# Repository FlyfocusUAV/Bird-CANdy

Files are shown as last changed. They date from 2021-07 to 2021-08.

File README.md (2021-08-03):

# Bird-CANdy

[][cc-by-sa] 

<hr>

PCB designed mainly as a universal [UAVCAN](https://uavcan.org/) sensor node which may also be used as a generic CAN interfacing device.

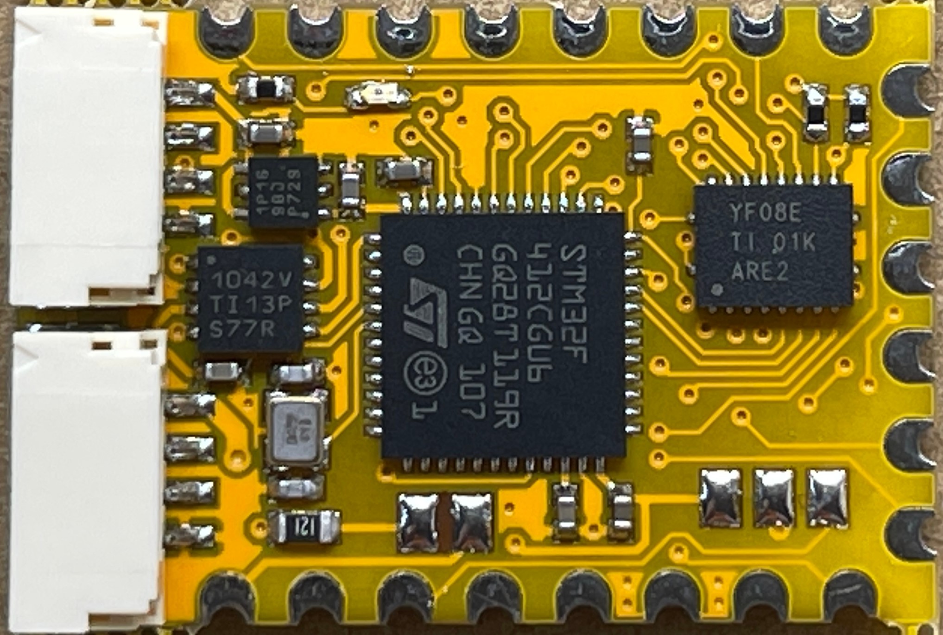
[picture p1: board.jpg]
Board top photo


<br>

# What's UAVCAN Node? #
UAVCAN Node is a device that speaks UAVCAN protocol which is usually used to exchange data between autopilot (e.g. The Cube or Pixhawk running Ardupilot software)
and peripherals like GPS, Compass, LEDs, etc.

Since UAVCAN uses CAN inteface it allows for much longer wires than in case of I2C/SPI/UART/etc. and interference free data exchange due to the use of differential pairs.

# Advantages of Bird CANdy PCB #
PCB was designed with hobbyist, DIYers and researchers in mind.
* Fully Open Source Hardware for non-commercial use
* Only 2 copper layers for cheap production
* 3.3V or 5V selectable outputs
* JST-GH connectors (fully compatible with [The Cube Autopilot](https://github.com/proficnc/The-Cube))
* Supports all [Ardupilot](https://ardupilot.org/) peripherals like GPS, Compass, Baro, IMU, LEDs, etc, as well as PWM Servo output.

# What about the software? #
PCB can run [AP_Periph](https://github.com/ArduPilot/ardupilot/tree/master/Tools/AP_Periph) or your own software written for STM32 microcontroller.

# Pinout #
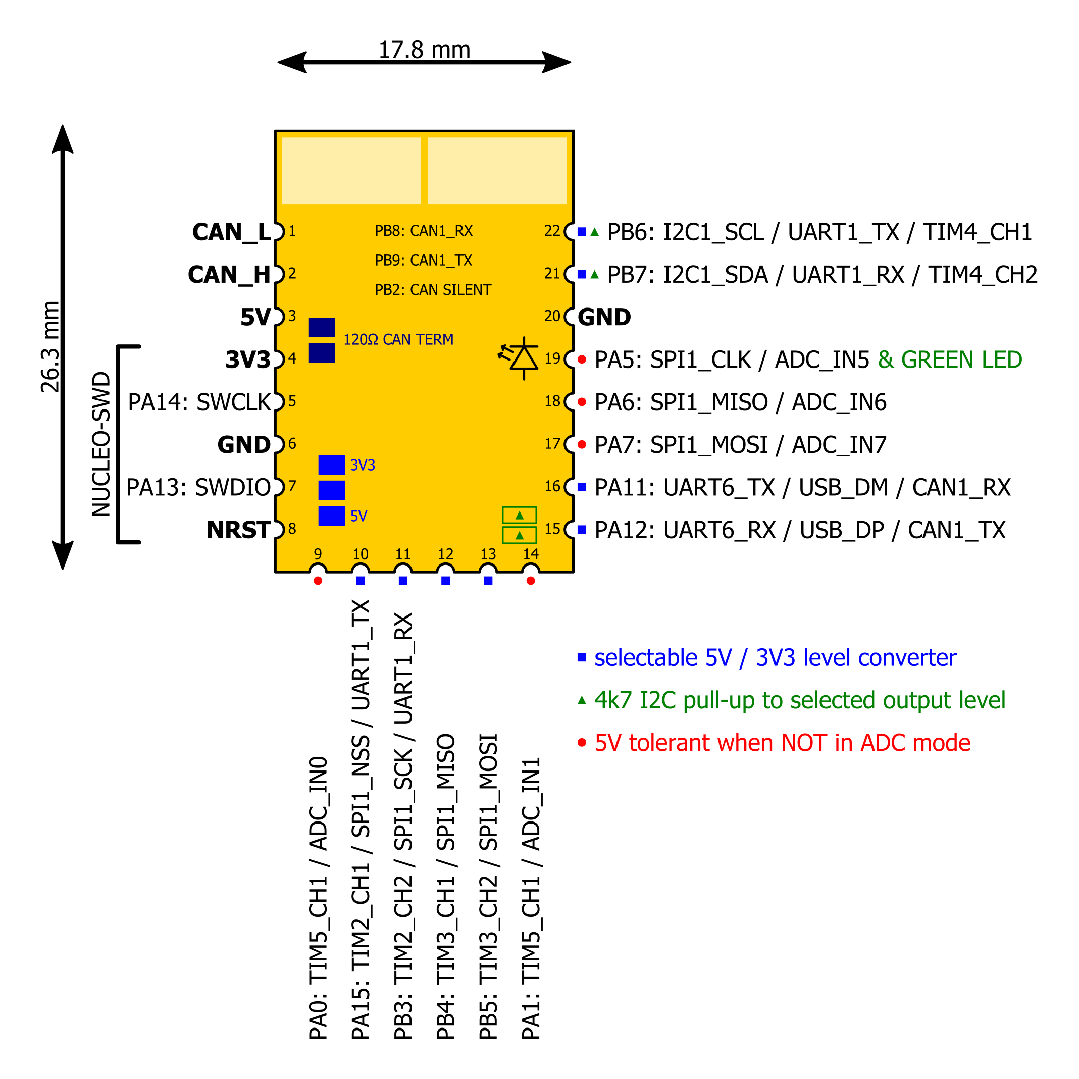
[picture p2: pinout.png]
Pinout guide


# Commercial license #
If You need a commercial license please send us an email to contact@flyfocus.pl 
<!-- <a href="https://www.linkedin.com/company/flyfocus/"> ![alt text](https://img.shields.io/badge/-LinkedIn-a8400e?style=flat&logo=linkedIn)</a>
<a href="https://www.facebook.com/flyfocusUAV"> ![alt text](https://img.shields.io/badge/-Facebook-a8400e?style=flat&logo=Facebook)</a> -->

[cc-by-sa]: https://creativecommons.org/licenses/by-sa/4.0/
[cc-by-shield]: https://img.shields.io/badge/License-CC%20BY%20%20SA%204.0-a8400e

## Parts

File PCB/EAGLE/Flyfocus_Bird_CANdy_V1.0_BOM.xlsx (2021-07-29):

Item # | Designator | QTY | Mfg Part # | Value/Description | Package
1 | C4,C5 | 2 | generic MLCC capacitor | 100n | 0402
2 | R1 | 1 | smd thick film >=0.2W resistor | 120R thick film: >=0.2W | 0603
3 | C2,C3 | 2 | generic MLCC capacitor | 10p | 0402
4 | C6, C7, C8 | 3 | generic MLCC capacitor | 1u | 0402
5 | U$1 | 1 | ABM11AIG-16.000MHZ-8-1Z-T or similar | 16MHZ | 2x1.6mm crystal
6 | C1,C9 | 2 | generic MLCC capacitor | 2u2 | 0402
7 | R2, R3 | 2 | generic smd resistor | 4k7 | 0402
8 | J1, J2 | 2 | SM04B-GHS-TB(LF)(SN) | JST-GH connector
9 | U1 | 1 | STM32F412CEU6/STM32F412CGU6 |  | 48-UFQFPN
10 | U2 | 1 | TJA1051TK/3/1J or TCAN1042HVDRBTQ1 |  | 8-VDFN
11 | U4 | 1 | TPS74633 |  | 6-WSON
12 | U3 | 1 | TXS0108ERGYR |  | 20-VFQFN
13 | D1 | 1 | generic 0402 LED - GREEN |  | 0402
14 | R4 | 1 | generic smd resistor | 33R | 0402

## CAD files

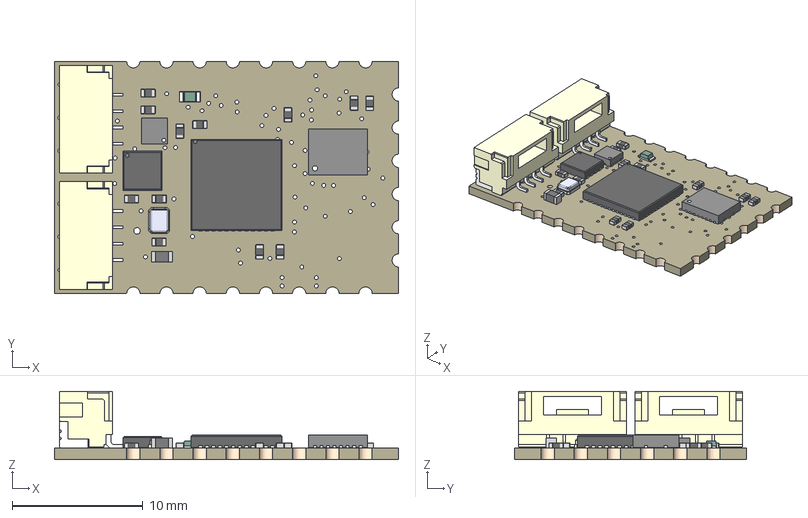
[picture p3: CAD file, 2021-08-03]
PCB/Flyfocus_Bird_CANdy_V1.0.step
26.3 x 17.8 x 5.22 mm
Board
STM32F412CEU6TRUFQFPN-48_7X7X0P55MM-M
SM04B-GHS-TB(LF)(SN)- x 2
TJA1051TK/3/1J
TPS74633PQWDRVRQ1
TXS0108ERGYR
Ferrite
Contact x 2
2X1.6_CRYSTAL
MA08-1
MA08-1 (1)
MA06-1
33R x 12
SJ
SJ_2

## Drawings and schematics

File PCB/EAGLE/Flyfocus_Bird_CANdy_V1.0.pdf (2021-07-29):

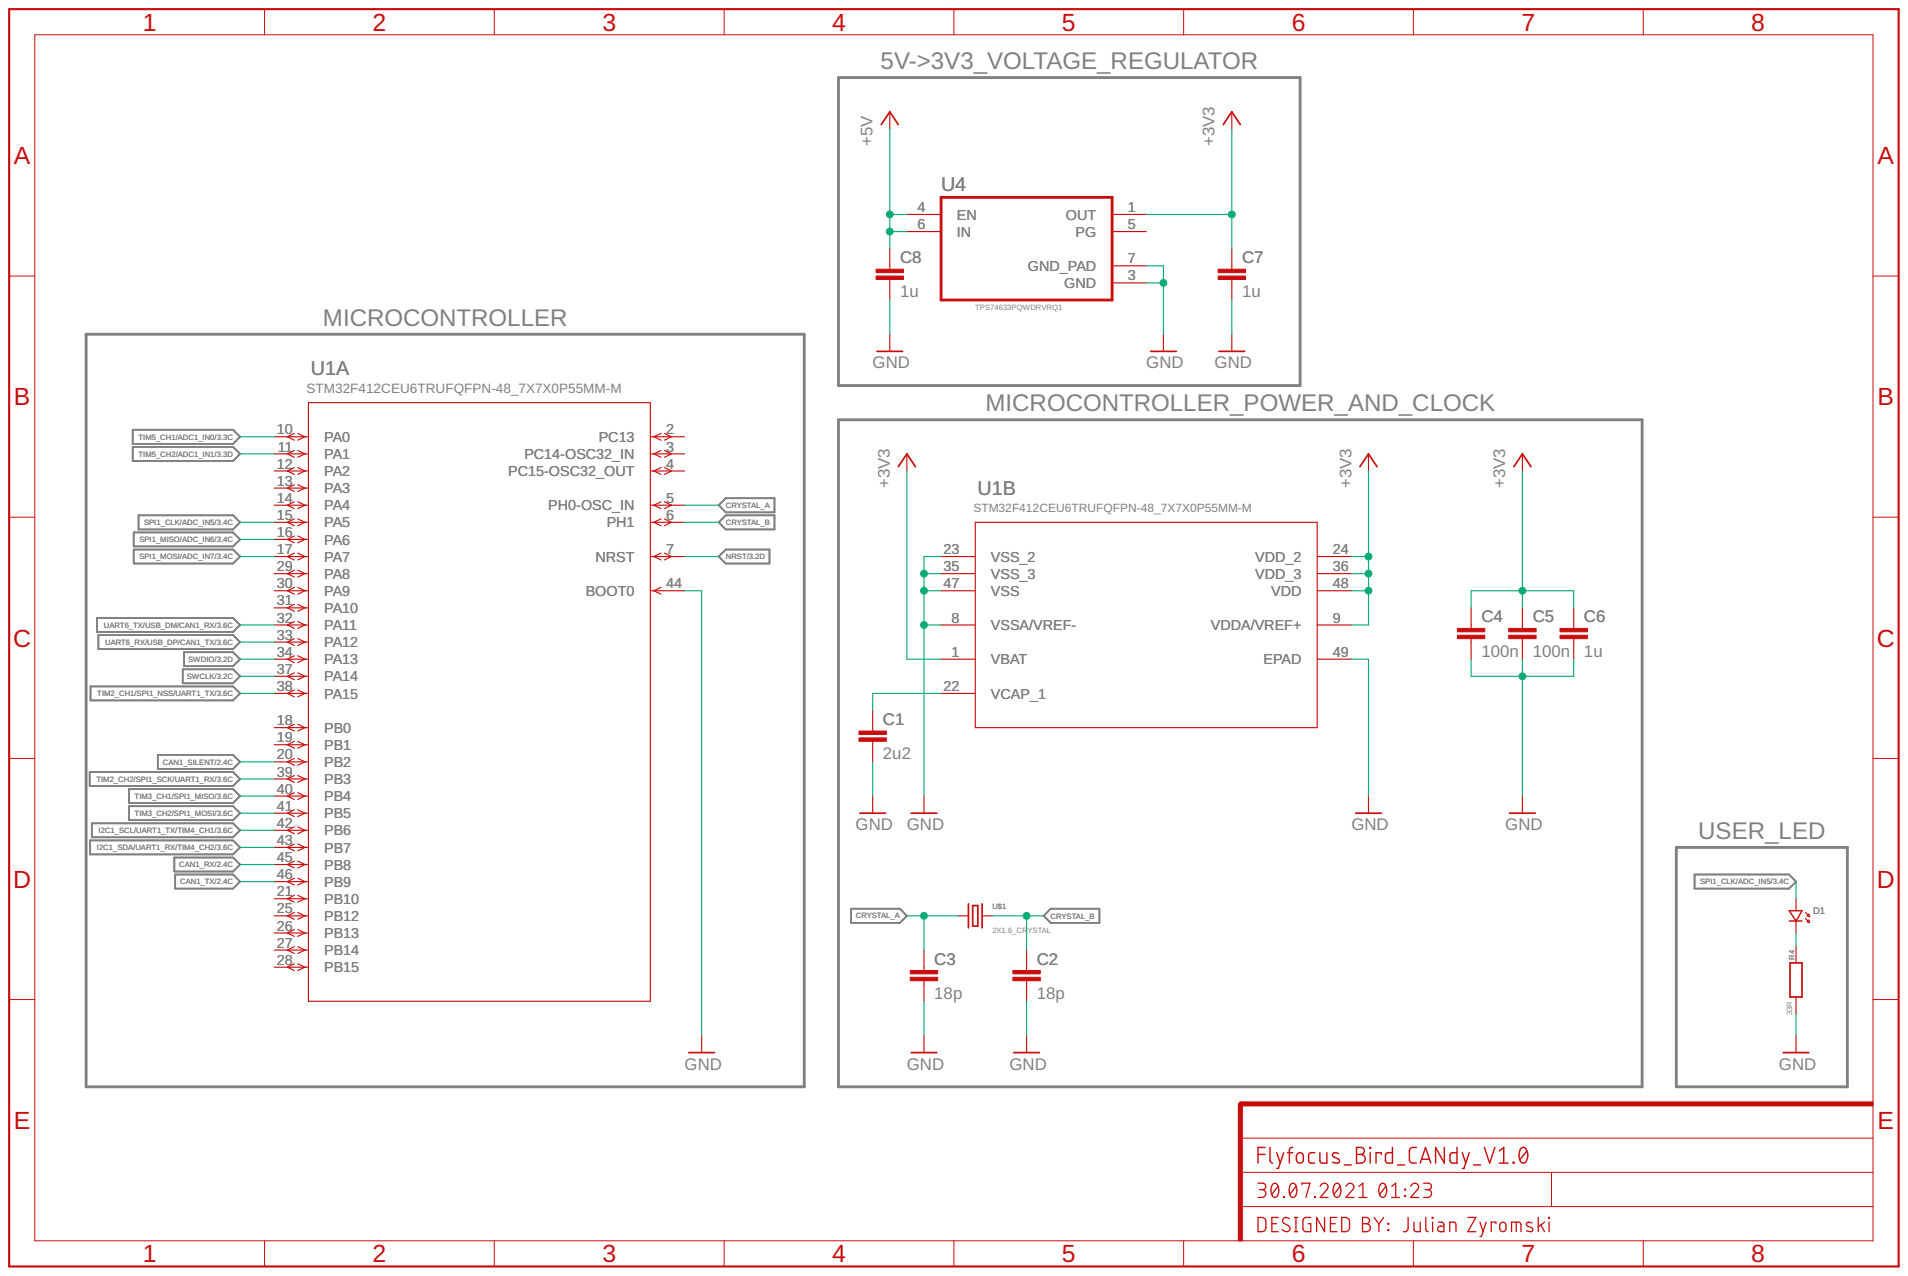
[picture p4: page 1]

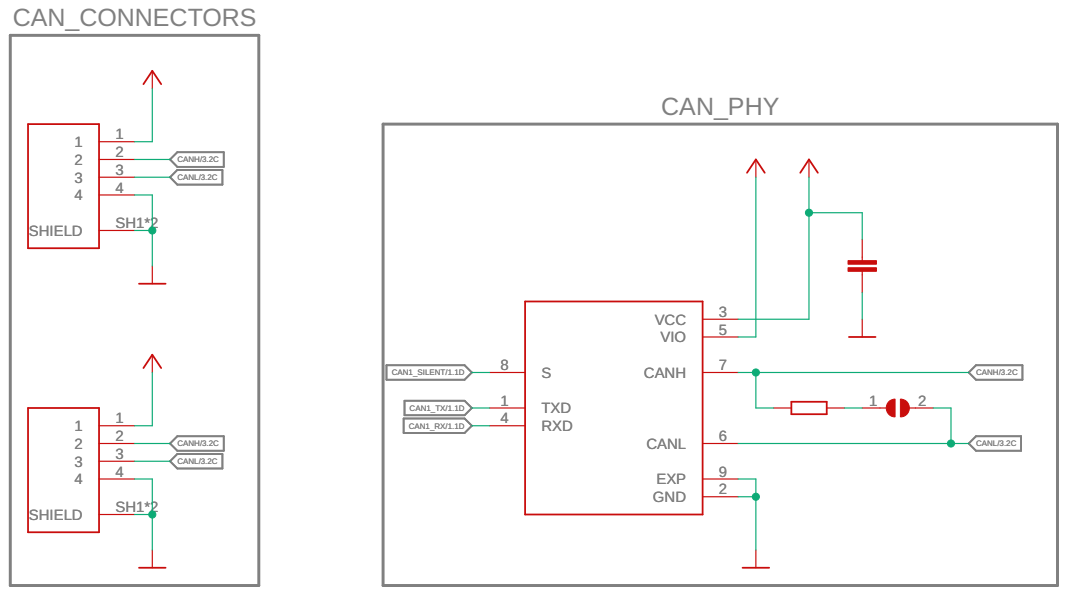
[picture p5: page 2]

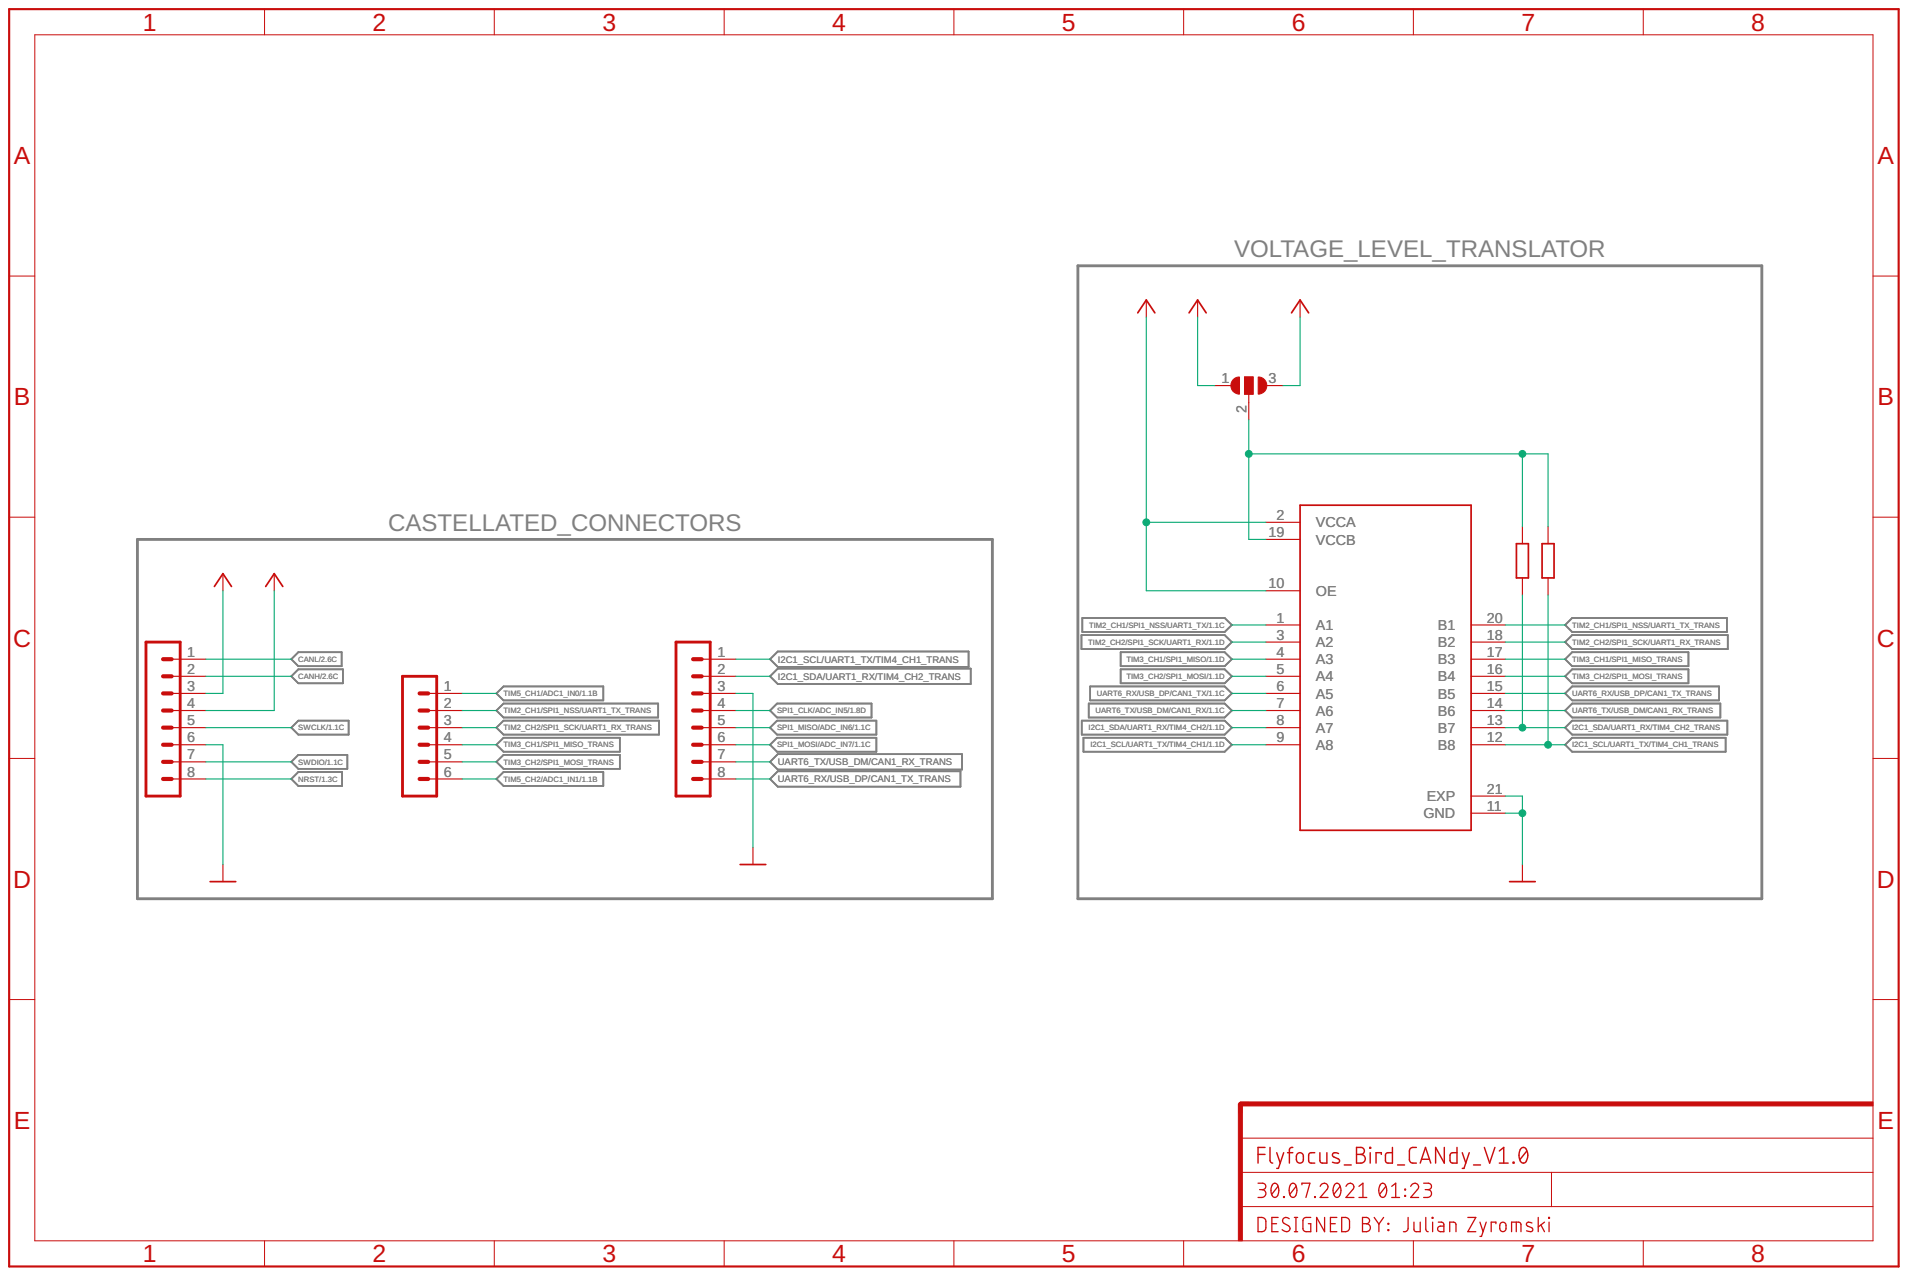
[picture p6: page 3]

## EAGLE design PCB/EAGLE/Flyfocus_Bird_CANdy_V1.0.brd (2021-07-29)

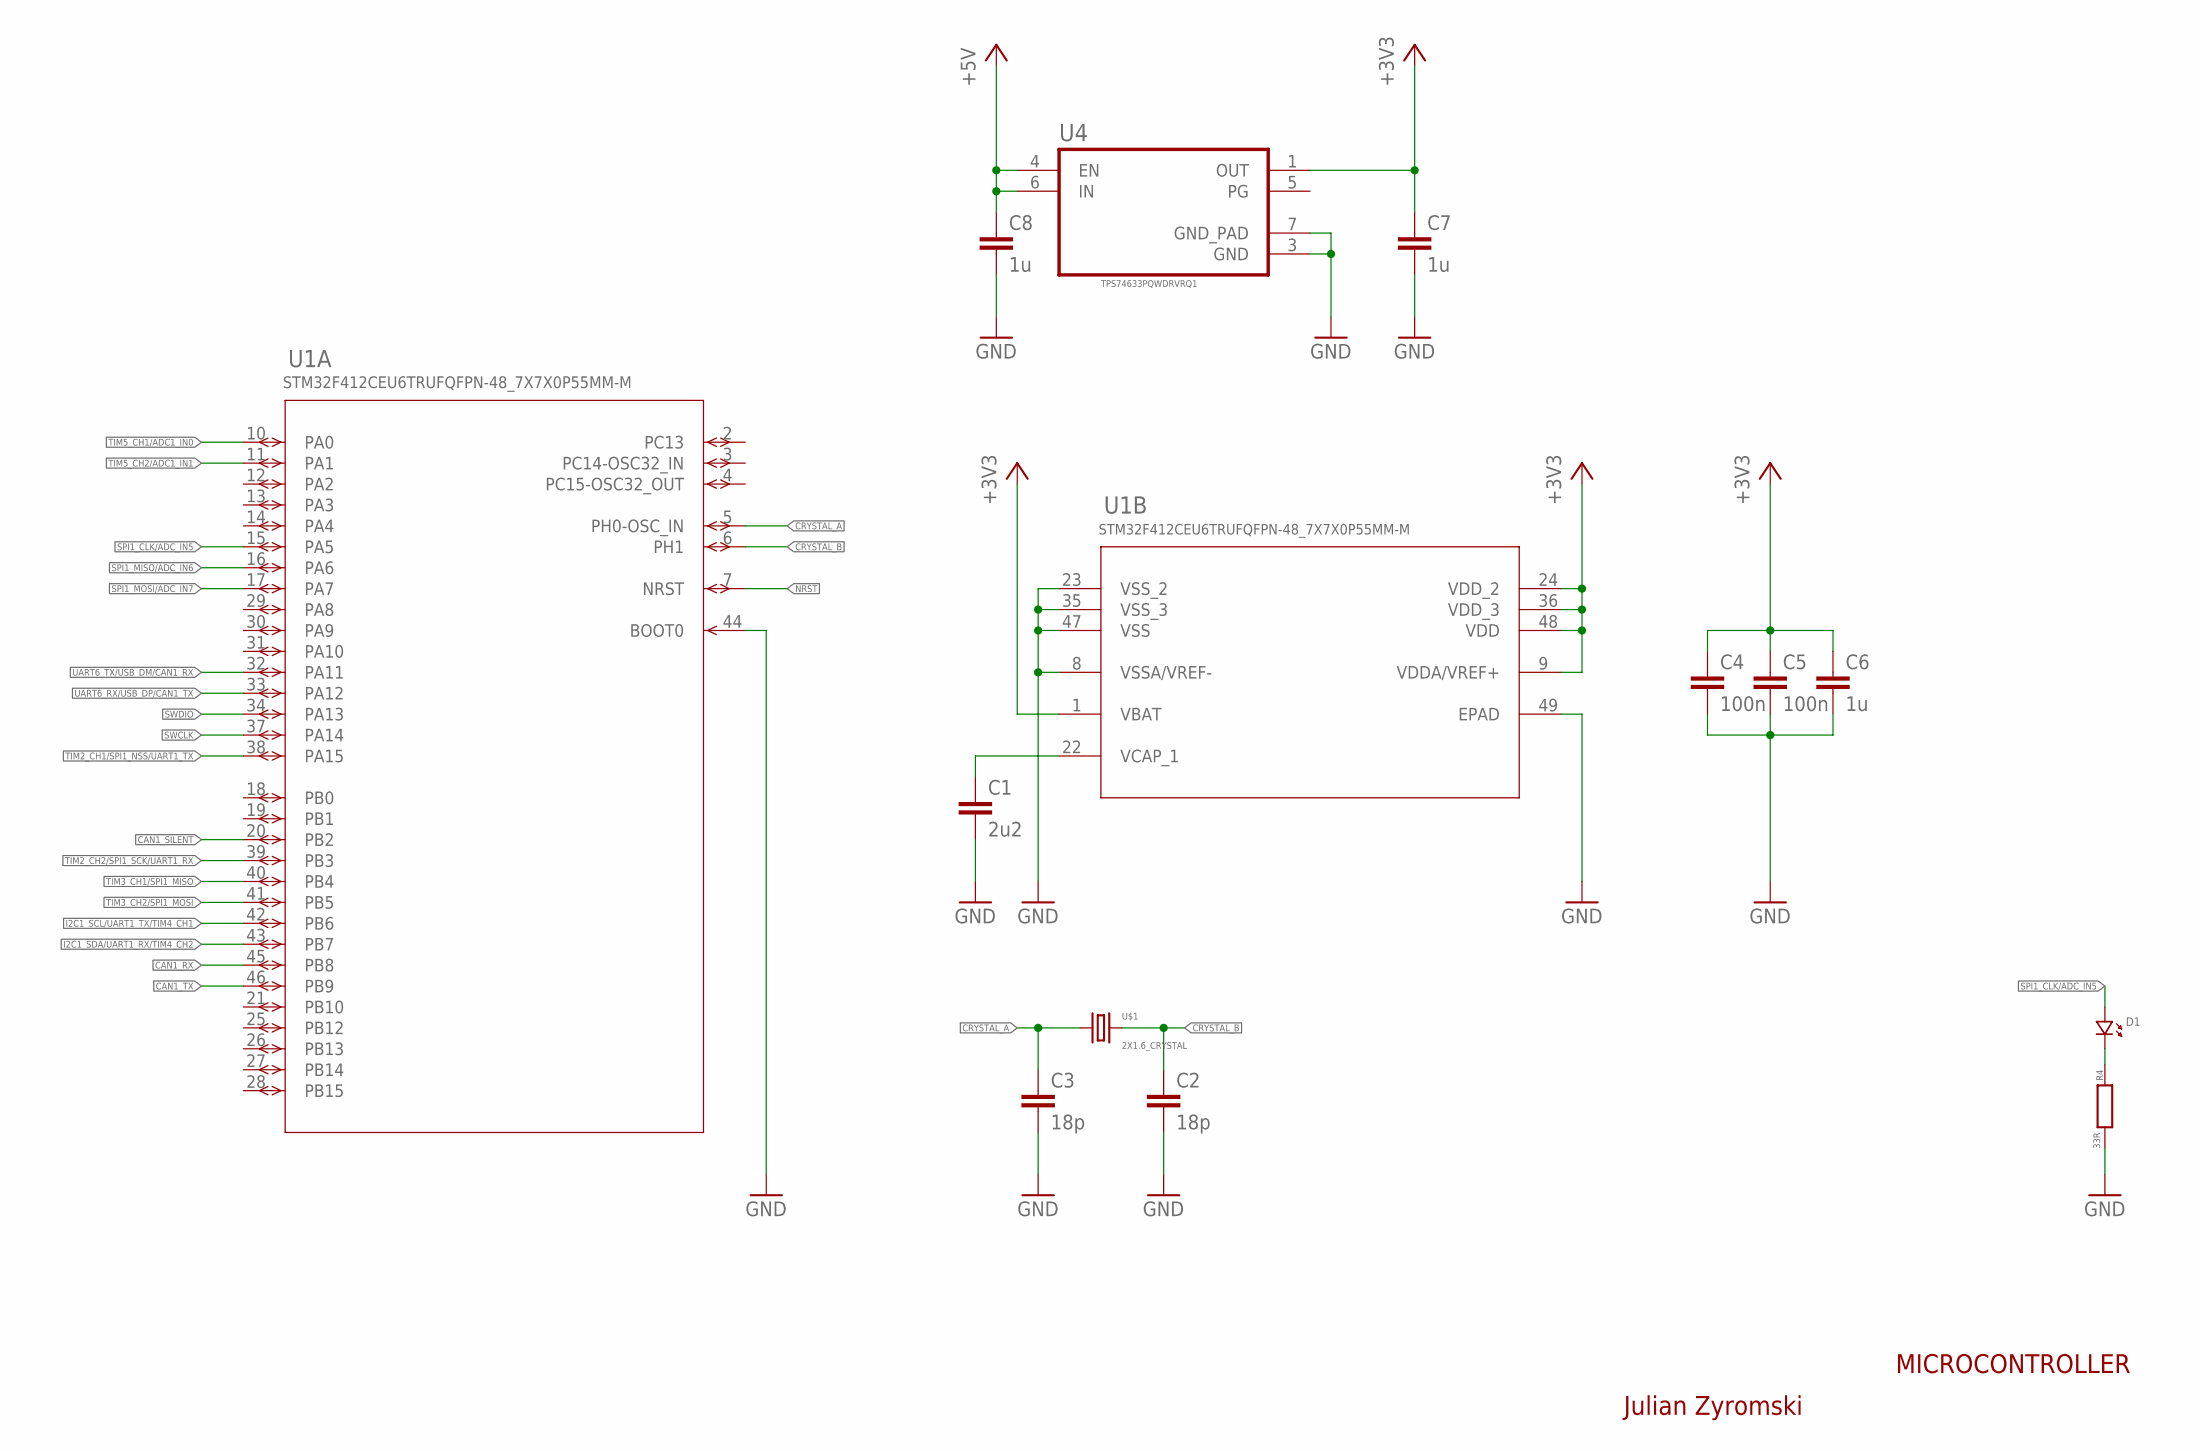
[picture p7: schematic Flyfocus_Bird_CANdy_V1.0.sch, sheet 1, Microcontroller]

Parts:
C1: 2u2; R0402
C2, C3: 18p; R0402
C4, C5: 100n; R0402
C6, C7, C8: 1u; R0402
D1: LED.0402; 0402.LED
R4: 33R; R0402
U1: STM32F412CEU6TRUFQFPN-48_7X7X0P55MM-M; UFQFPN-48_7X7X0P55MM-M
U4: TPS74633PQWDRVRQ1; SON65P200X200X80-7N
U$1: 2X1.6_CRYSTAL; OSC_FA-128_16MHZ

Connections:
+3V3: C4.1, C5.1, C6.1, C7.1, U1.1 (VBAT), U1.9 (VDDA/VREF+), U1.24 (VDD_2), U1.36 (VDD_3), U1.48 (VDD), U4.1 (OUT); also elsewhere on the board
+5V: C8.1, U4.4 (EN), U4.6 (IN); also elsewhere on the board
CAN1_RX: U1.45 (PB8); also elsewhere on the board
CAN1_SILENT: U1.20 (PB2); also elsewhere on the board
CAN1_TX: U1.46 (PB9); also elsewhere on the board
CRYSTAL_A: C3.1, U1.5 (PH0-OSC_IN), U$1.1
CRYSTAL_B: C2.1, U1.6 (PH1), U$1.3 (2)
GND: C1.2, C2.2, C3.2, C4.2, C5.2, C6.2, C7.2, C8.2, R4.2, U1.8 (VSSA/VREF-), U1.23 (VSS_2), U1.35 (VSS_3), U1.44 (BOOT0), U1.47 (VSS), U1.49 (EPAD), U4.3 (GND), U4.7 (GND_PAD); also elsewhere on the board
I2C1_SCL/UART1_TX/TIM4_CH1: U1.42 (PB6); also elsewhere on the board
I2C1_SDA/UART1_RX/TIM4_CH2: U1.43 (PB7); also elsewhere on the board
unnamed: C1.1, U1.22 (VCAP_1)
unnamed: D1.P$2 (2), R4.1
NRST: U1.7 (NRST); also elsewhere on the board
SPI1_CLK/ADC_IN5: D1.P$1 (1), U1.15 (PA5); also elsewhere on the board
SPI1_MISO/ADC_IN6: U1.16 (PA6); also elsewhere on the board
SPI1_MOSI/ADC_IN7: U1.17 (PA7); also elsewhere on the board
SWCLK: U1.37 (PA14); also elsewhere on the board
SWDIO: U1.34 (PA13); also elsewhere on the board
TIM2_CH1/SPI1_NSS/UART1_TX: U1.38 (PA15); also elsewhere on the board
TIM2_CH2/SPI1_SCK/UART1_RX: U1.39 (PB3); also elsewhere on the board
TIM3_CH1/SPI1_MISO: U1.40 (PB4); also elsewhere on the board
TIM3_CH2/SPI1_MOSI: U1.41 (PB5); also elsewhere on the board
TIM5_CH1/ADC1_IN0: U1.10 (PA0); also elsewhere on the board
TIM5_CH2/ADC1_IN1: U1.11 (PA1); also elsewhere on the board
UART6_RX/USB_DP/CAN1_TX: U1.33 (PA12); also elsewhere on the board
UART6_TX/USB_DM/CAN1_RX: U1.32 (PA11); also elsewhere on the board

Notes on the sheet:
Julian Zyromski
MICROCONTROLLER

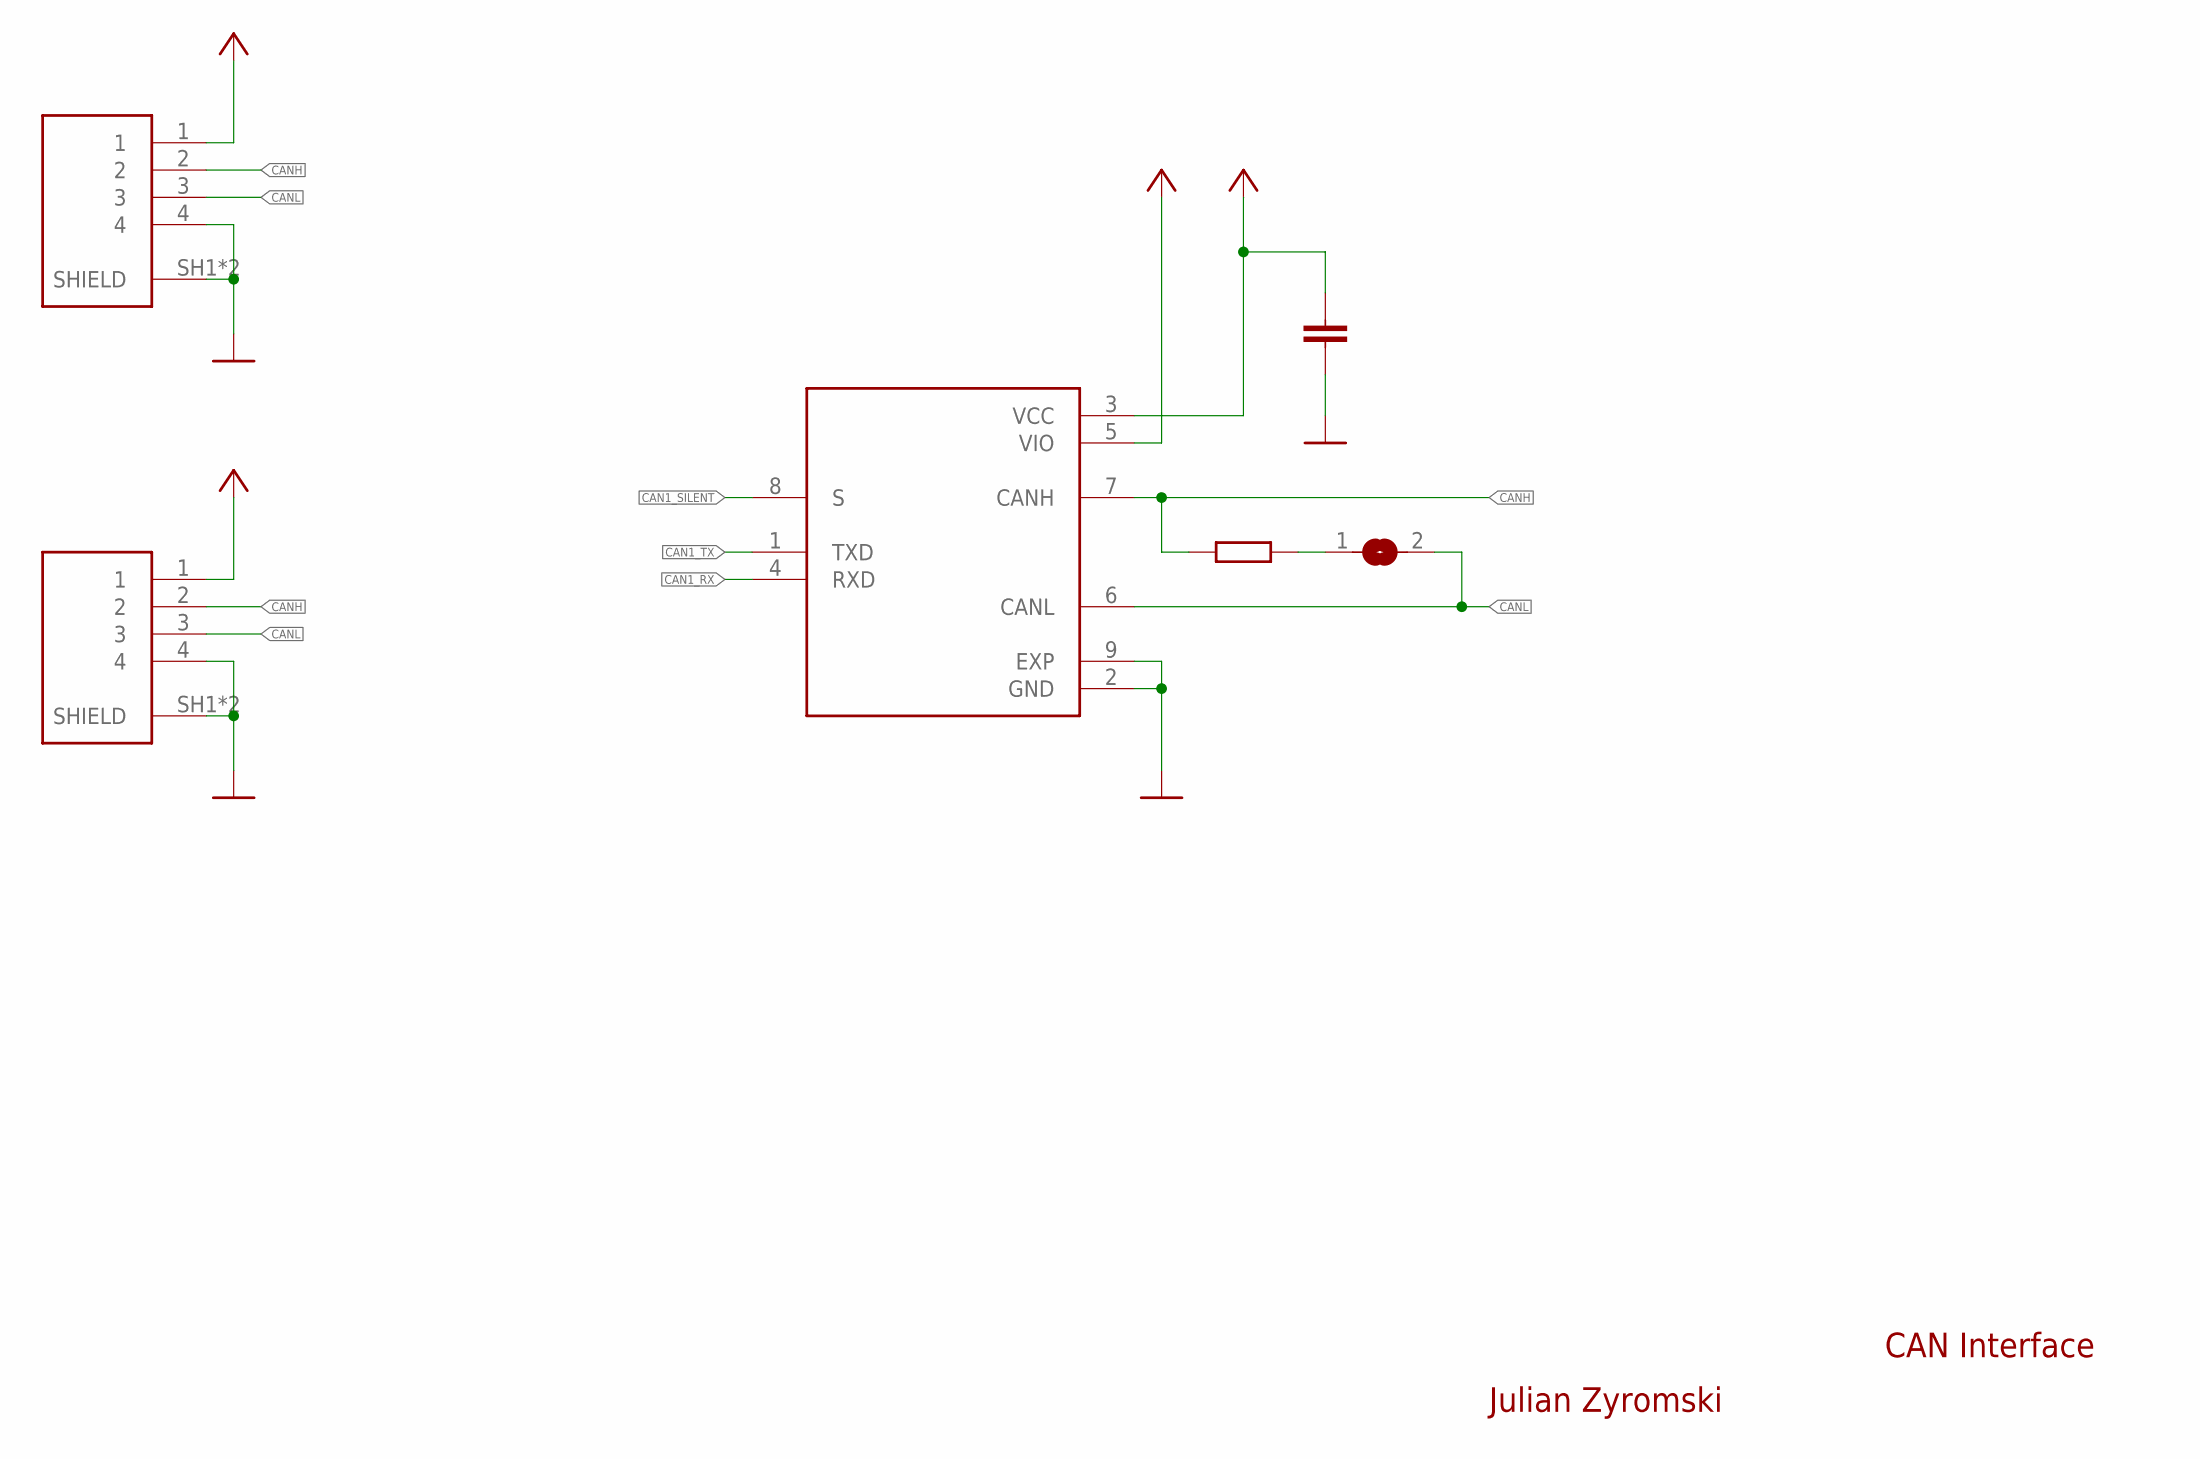
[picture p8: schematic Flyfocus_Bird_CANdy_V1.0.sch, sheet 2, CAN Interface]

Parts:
C9: 2u2; R0402
J1, J2: SM04B-GHS-TB(LF)(SN)-; JST_SM04B-GHS-TB(LF)(SN)-
R1: 120R/thick_film; 0603
SJ1: SJ
U2: TJA1051TK/3/1J; SON65P300X300X95-8N

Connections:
+3V3: U2.5 (VIO); also elsewhere on the board
+5V: C9.1, J1.1, J2.1, U2.3 (VCC); also elsewhere on the board
CAN1_RX: U2.4 (RXD); also elsewhere on the board
CAN1_SILENT: U2.8 (S); also elsewhere on the board
CAN1_TX: U2.1 (TXD); also elsewhere on the board
CANH: J1.2, J2.2, R1.P$1 (1), U2.7 (CANH); also elsewhere on the board
CANL: J1.3, J2.3, SJ1.2, U2.6 (CANL); also elsewhere on the board
GND: C9.2, J1.4, J1.SH1 (SHIELD), J1.SH2 (SHIELD), J2.4, J2.SH1 (SHIELD), J2.SH2 (SHIELD), U2.2 (GND), U2.9 (EXP); also elsewhere on the board
unnamed: R1.P$2 (2), SJ1.1

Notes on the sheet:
Julian Zyromski
CAN Interface

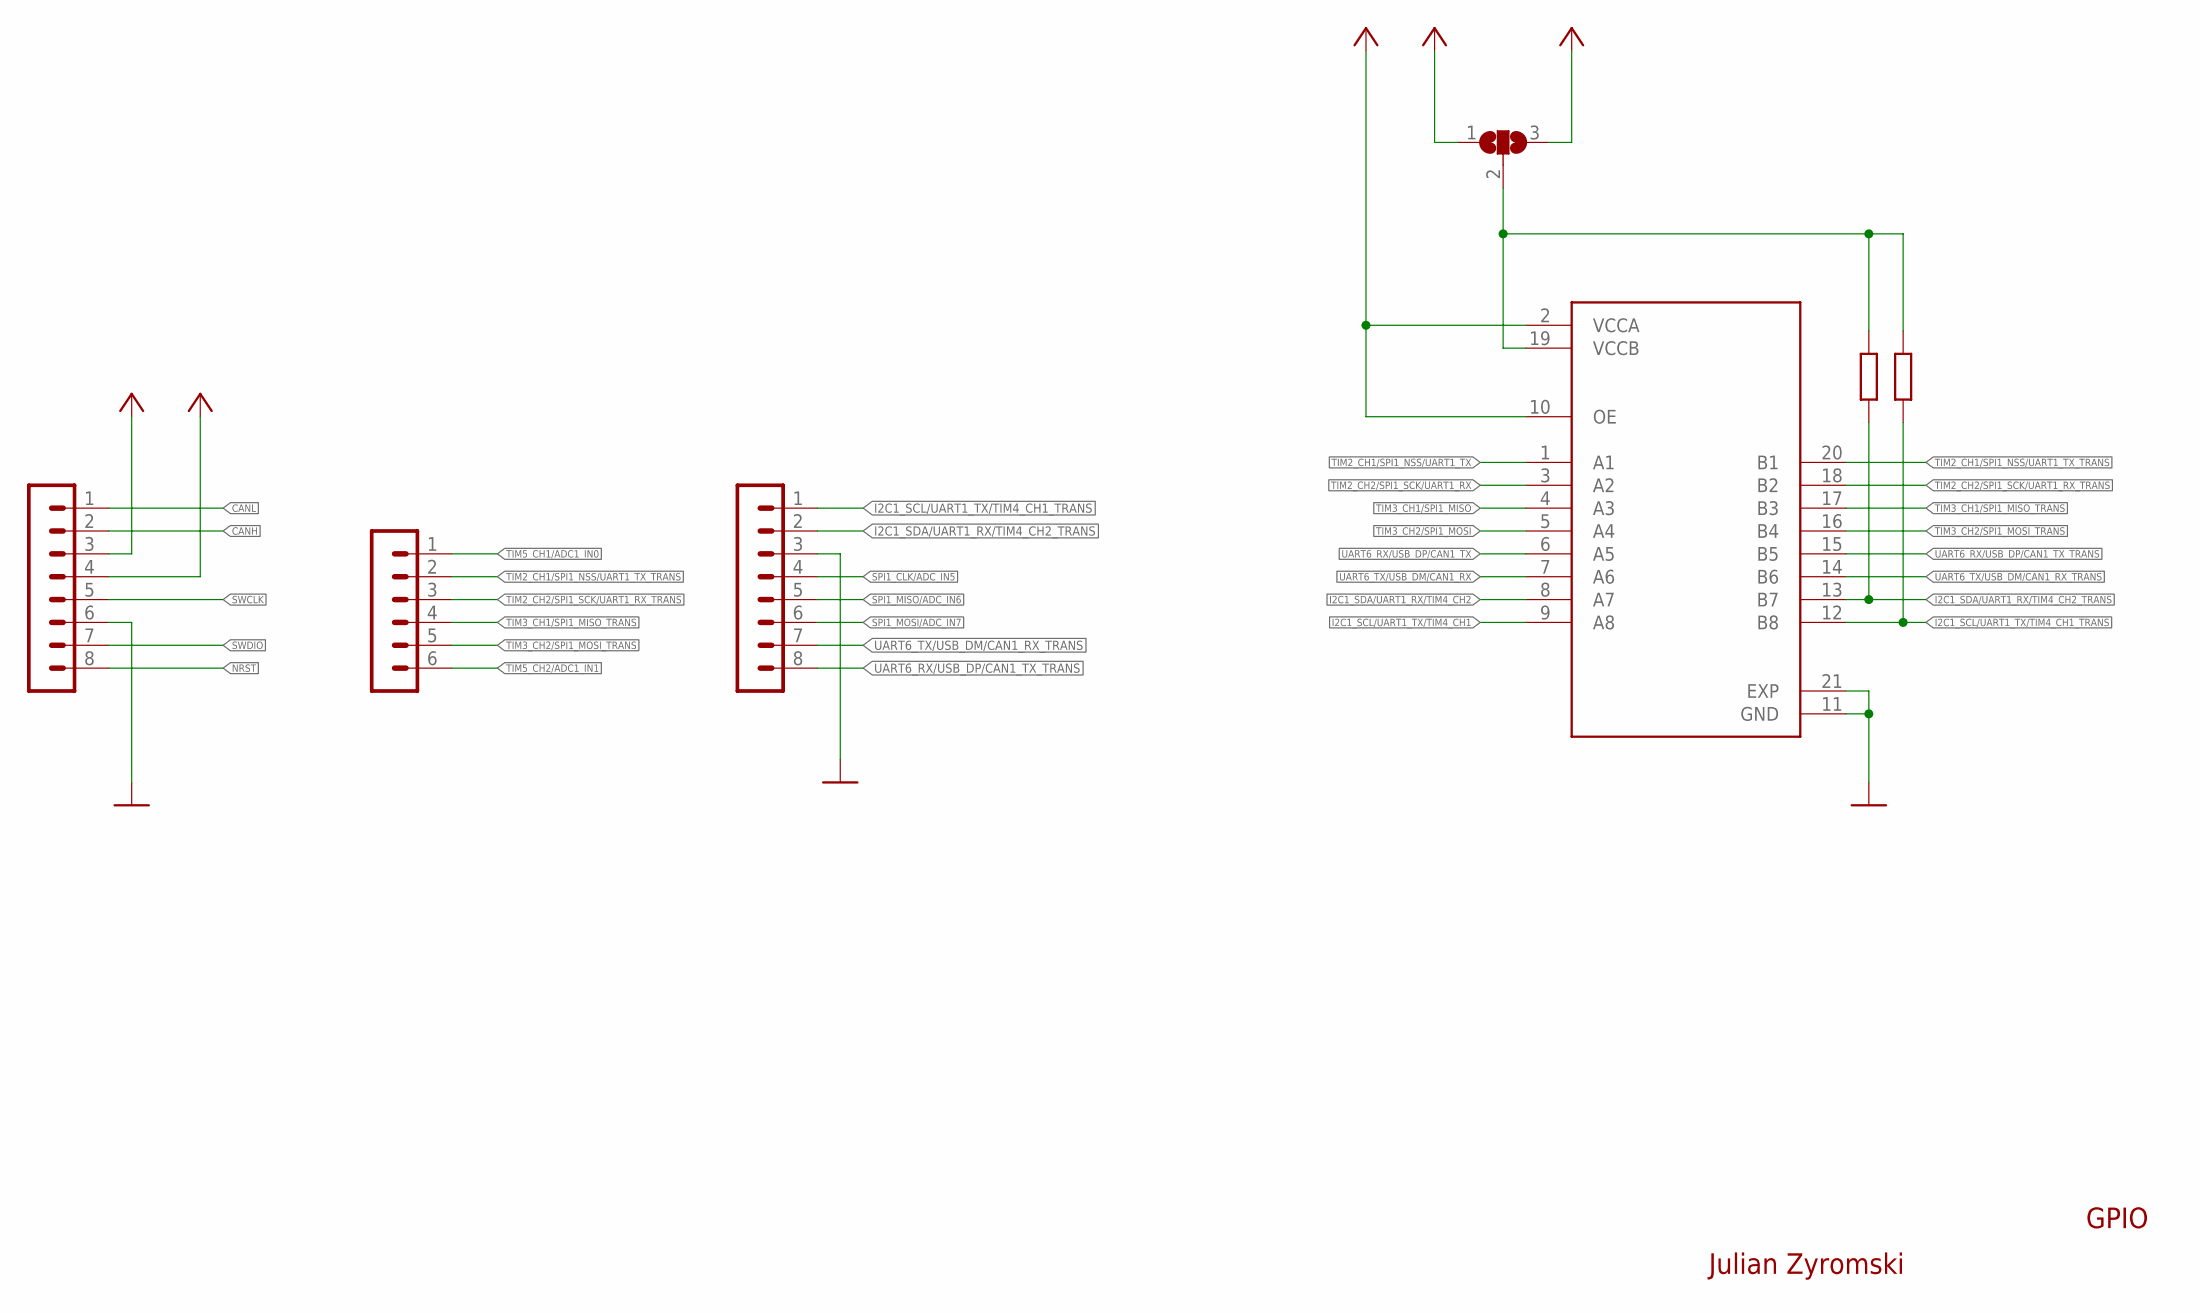
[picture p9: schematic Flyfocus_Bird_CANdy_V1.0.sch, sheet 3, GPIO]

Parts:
R2, R3: 4k7; R0402
SJ2: SJ2W; SJ_2
SV1, SV2: MA08-1
SV3: MA06-1
U3: TXS0108ERGYR; IC_TXS0108ERGYR

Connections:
+3V3: SJ2.1, SV1.4, U3.2 (VCCA), U3.10 (OE); also elsewhere on the board
+5V: SJ2.3, SV1.3; also elsewhere on the board
CANH: SV1.2; also elsewhere on the board
CANL: SV1.1; also elsewhere on the board
GND: SV1.6, SV2.3, U3.11 (GND), U3.21 (EXP); also elsewhere on the board
I2C1_SCL/UART1_TX/TIM4_CH1: U3.9 (A8); also elsewhere on the board
I2C1_SCL/UART1_TX/TIM4_CH1_TRANS: R3.1, SV2.1, U3.12 (B8)
I2C1_SDA/UART1_RX/TIM4_CH2: U3.8 (A7); also elsewhere on the board
I2C1_SDA/UART1_RX/TIM4_CH2_TRANS: R2.1, SV2.2, U3.13 (B7)
unnamed: R2.2, R3.2, SJ2.2, U3.19 (VCCB)
NRST: SV1.8; also elsewhere on the board
SPI1_CLK/ADC_IN5: SV2.4; also elsewhere on the board
SPI1_MISO/ADC_IN6: SV2.5; also elsewhere on the board
SPI1_MOSI/ADC_IN7: SV2.6; also elsewhere on the board
SWCLK: SV1.5; also elsewhere on the board
SWDIO: SV1.7; also elsewhere on the board
TIM2_CH1/SPI1_NSS/UART1_TX: U3.1 (A1); also elsewhere on the board
TIM2_CH1/SPI1_NSS/UART1_TX_TRANS: SV3.2, U3.20 (B1)
TIM2_CH2/SPI1_SCK/UART1_RX: U3.3 (A2); also elsewhere on the board
TIM2_CH2/SPI1_SCK/UART1_RX_TRANS: SV3.3, U3.18 (B2)
TIM3_CH1/SPI1_MISO: U3.4 (A3); also elsewhere on the board
TIM3_CH1/SPI1_MISO_TRANS: SV3.4, U3.17 (B3)
TIM3_CH2/SPI1_MOSI: U3.5 (A4); also elsewhere on the board
TIM3_CH2/SPI1_MOSI_TRANS: SV3.5, U3.16 (B4)
TIM5_CH1/ADC1_IN0: SV3.1; also elsewhere on the board
TIM5_CH2/ADC1_IN1: SV3.6; also elsewhere on the board
UART6_RX/USB_DP/CAN1_TX: U3.6 (A5); also elsewhere on the board
UART6_RX/USB_DP/CAN1_TX_TRANS: SV2.8, U3.15 (B5)
UART6_TX/USB_DM/CAN1_RX: U3.7 (A6); also elsewhere on the board
UART6_TX/USB_DM/CAN1_RX_TRANS: SV2.7, U3.14 (B6)

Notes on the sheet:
Julian Zyromski
GPIO

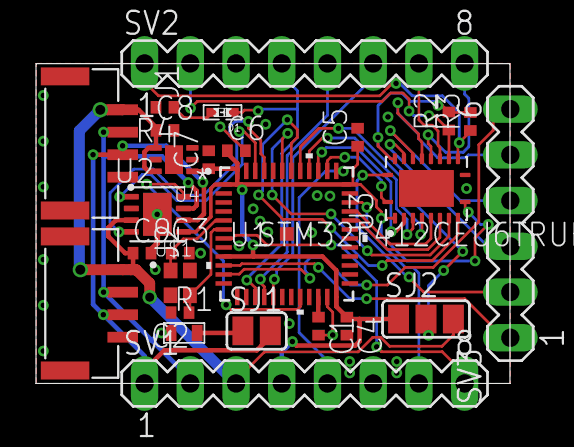
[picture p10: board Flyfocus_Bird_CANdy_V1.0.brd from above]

Board: 2 copper layers, 26.3 x 17.8 mm, 26 parts (0 on the bottom side), 38 nets.

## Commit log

2021-07-29 added eagle files and pdf schematic
    [Flyfocus_Bird_CANdy_V1.0.brd, Flyfocus_Bird_CANdy_V1.0.sch]
2021-07-29 Added PCB production files
    [Flyfocus_Bird_CANdy_V1.0_BOM.xlsx]
2021-07-29 KiCad init
2021-08-03 added 3D files, readme update
    [Flyfocus_Bird_CANdy_V1.0.step]

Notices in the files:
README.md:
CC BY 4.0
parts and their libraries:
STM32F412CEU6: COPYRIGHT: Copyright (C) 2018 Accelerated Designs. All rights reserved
